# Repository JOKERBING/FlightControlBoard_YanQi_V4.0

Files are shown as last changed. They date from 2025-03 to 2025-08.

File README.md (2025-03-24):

# YanQi Flight Control Board V4.0

**2 x IMU & Baro & 4 x ESC small size PX4 for MAV research.**

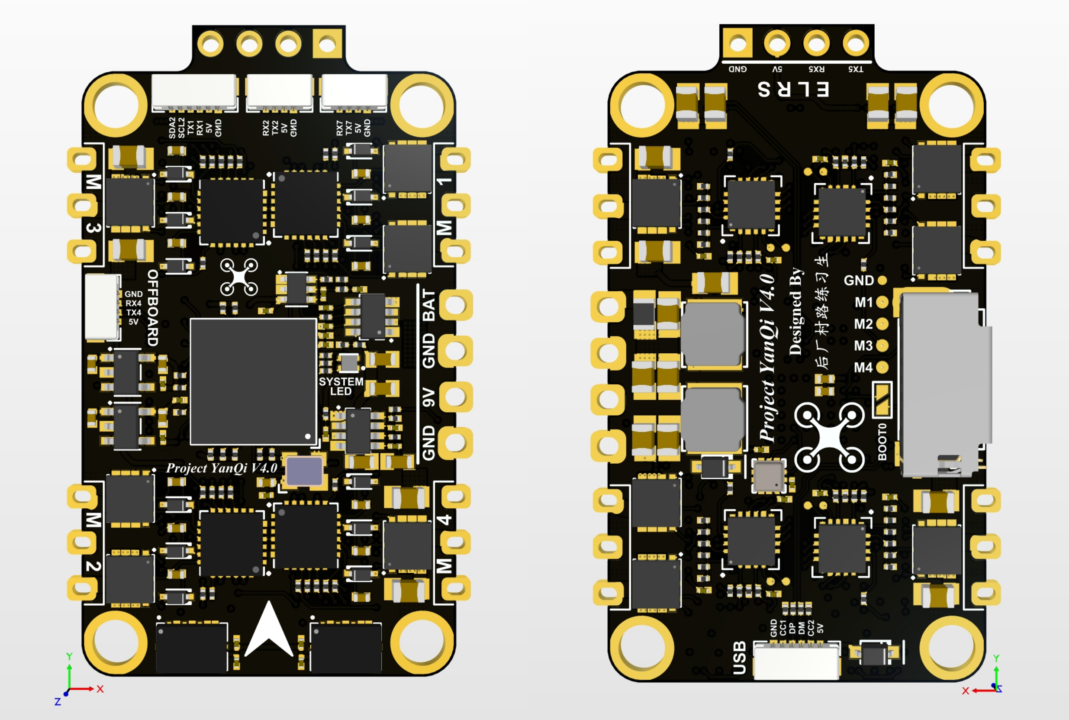
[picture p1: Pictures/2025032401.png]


## Physical

- Mounting: 20 x 35 mm, Φ 2 mm
- Dimensions: 24 x 42.4 x 6 mm
- Weight: 4.9 g

## Specifications

- MCU: STM32H743VIH6, 480MHz, 2MB Flash
- IMU: BMI088 + BMI088
- Baro: BMP388
- ESC: 4 x Bluejay
- MicroSD Card Slot
- USB
- 5 x UART
- 4 x PWM (DShot)
- 1 x External I2C
- 2 x ADC (Battery Voltage, Battery Current)
- BEC 9V 3A output
- BEC 5V 3A output

## UART Mapping

<div align="center">

| UART | TTY | SerialName | Suggest Funcion | DMA |
| :--: | :-: | :---: | :---: | :-: |
| USART1 | /dev/ttyS0 | GPS1 | GPS | OFF |
| USART2 | /dev/ttyS1 | TEL1 | Data Link | ON |
| UART4 | /dev/ttyS3 | TEL2 | Offboard PC | ON |
| UART5 | /dev/ttyS4 |  RC  | ELRS Receiver | ON |
| UART7 | /dev/ttyS6 | TEL3 | Optical Flow | ON |

</div>

## Getting Start

### Compile Locally

Follow the PX4 standard approach.

#### Bootloader:

```shell
make UCAS_YanQiH7_bootloader
```

#### Firmware:

```shell
make UCAS_YanQiH7_default
```

### Burn Bootloader & Firmware

#### Bootloader:

**Method 1：**

 To enter DFU mode, pull up BOOT0 while connecting the USB cable to your computer.

```shell
make UCAS_YanQiH7_bootloader upload
```

**Method 2：**

 To enter DFU mode, pull up BOOT0 while connecting the USB cable to your computer.

```shell
dfu-util -a 0 --dfuse-address 0x08000000 -D ./build/UCAS_YanQiH7_bootloader/UCAS_YanQiH7_bootloader.bin
```

If the burning tool is not installed, install the dfu util burning toolkit first.

```
sudo apt install dfu-util
```

#### Firmware:

**Method 1：**

```shell
make UCAS_YanQiH7_default upload
```

Connect the flight controller directly to your computer via USB.

The firmware will then proceed through a number of upgrade steps (downloading new firmware, erasing old firmware etc.). Each step is printed to the screen.

Once the firmware has completed loading, the device/vehicle will reboot and reconnect.

**Method 2：**

Start QGroundControl and connect the vehicle.

Select **"Q" icon** > **Vehicle Setup** > **Firmware** (sidebar) to open Firmware Setup.

Connect the flight controller directly to your computer via USB.

Check **Advanced settings** and select the version from the dropdown list.

Select the **Custom Firmware file...** option to install the custom firmware for the flight controller (autodetected).

Click the **OK** button to start the update.

The firmware will then proceed through a number of upgrade steps (downloading new firmware, erasing old firmware etc.). Each step is printed to the screen and overall progress is displayed on a progress bar.

Once the firmware has completed loading, the device/vehicle will reboot and reconnect.

## Setting Up PX4 Configuration Settings

### Power

### MAVLink

### Receiver

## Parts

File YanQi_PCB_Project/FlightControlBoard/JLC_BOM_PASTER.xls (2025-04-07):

型号 | 封装 | 位号 | 元件编号
BMI088 | LGA-16_L4.5-W3.0-P0.50-BL | U10,U11 | C194919
RT9013-33GB | SOT-23-5 | U15,U16 | C47773
MP2225GJ-Z | SOT-23-8 | U13,U14 | C133066
STM32H743VIH6 | BGA-100_L8.0-W8.0-P0.80-R10-C10-BL | U1 | C964146
1nF | C0201 | C52 | C161371
1uF | C0402 | C17,C18,C19,C20,C21,C22,C23,C24,C25,C26,C27,C28,C45,C46,C48,C49 | C52923
140kΩ | R0201 | R89 | C158804
1N5819WS | SOD-323 | D13,D14 | C191023
X1G004171002700 | OSC-SMD_4P-L2.5-W2.0-BL | X1 | C255993
INA199A1DCKR | SOT-323-6 | U17 | C59135
2.2uF | C0402 | C2,C3 | C342966
SM04B-XSRS-ETB(LF)(SN) | CONN-SMD_4P-P0.6 | J3,J5,J6 | C5223639
1kΩ | R0201 | R6,R7,R8,R9 | C138165
56Ω | R0201 | R95 | C320971
FC-B1010RGBT-HG | LED-ARRAY-SMD_4P-L1.0-W1.0-TR-RD | LED1 | C158099
22uF | C0603 | C36,C37,C38,C39 | C2762594
FD6288Q | QFN-24_L4.0-W4.0-P0.50-BL-EP2.6 | U6,U7,U8,U9 | C328453
100nF | C0201 | C5,C7,C8,C9,C10,C11,C12,C13,C14,C15,C16,C29,C30,C31,C32,C33,C34,C35,C40,C41,C42,C43,C44,C47,C50,C51 | C160831
BMP388 | LGA-10 | U12 | C779278
AON7934 | DFN-8 | Q1,Q2,Q3,Q4,Q5,Q6,Q7,Q8,Q9,Q10,Q11,Q12 | C485677
22uF | C0805 | C53,C54,C55,C56,C57,C58,C59,C60,C61,C62,C63,C64,C65,C66,C67,C68,C69,C70 | C45783
10mΩ | R0805 | R96 | C163089
22Ω | R0201 | R50,R51,R52,R53,R54,R55,R56,R57,R58,R59,R60,R61,R62,R63,R64,R65,R66,R67,R68,R69,R70,R71,R72,R73,R85,R86 | C155743
74kΩ | R0201 | R90 | C851792
SM06B-XSRS-ETB(LF)(SN) | CONN-SMD_6P-P0.6 | J1,J2 | C5306600
5.1kΩ | R0201 | R83,R84 | C274341
100kΩ | R0201 | R91,R92,R94 | C270364
TF-027-H300 | TF-SMD_HYCW104-TF08-375B | SD1 | C5310495
FHD4020S-100MT | IND-SMD_L4.0-W4.0 | L1 | C602032
FHD4020S-4R7MT | IND-SMD_L4.0-W4.0 | L2 | C602031
10kΩ | R0201 | R1,R2,R3,R4,R5,R10,R11,R12,R13,R14,R15,R16,R17,R18,R19,R20,R21,R22,R23,R24,R25,R78,R79,R80,R81,R82,R87,R88,R93 | C473048
4.7kΩ | R0201 | R27,R29,R31,R33,R35,R37,R39,R41,R43,R45,R47,R49,R74,R75,R76,R77 | C270346
15pF | C0201 | C6 | C161407
1uF | C0201 | C4 | C237278
47kΩ | R0201 | R26,R28,R30,R32,R34,R36,R38,R40,R42,R44,R46,R48 | C270345
4.7uF | C0402 | C1 | C23733
EFM8BB21F16G | QFN-20_L3.0-W3.0-P0.50-BL-EP1.7_EFM8BB21F16G | U2,U3,U4,U5 | C80713
1N4148WTT4 | SOD-523 | D1,D2,D3,D4,D5,D6,D7,D8,D9,D10,D11,D12 | C68948
BurnPad | BURNPAD_0.8MM | P10,P11,P12,P13 | NC
ShortCircuitPad | SHORTCIRCUITPAD | P1 | NC
M3_HOLE | M3_HOLE | H1,H2,H3,H4 | NC
MotorPad | MOTORHALFHOLE | P14,P15,P16,P17,P18,P19,P20,P21,P22,P23,P24,P25 | NC
Power_Pad | POWERHALFHOLE | P26,P27,P28,P29 | NC
型号 | 封装 | 位号 | NC
ZX-SH1.0-4PWT | ELRSPAD | J4 | NC
BurnPad | BURNPAD_0.5MM | P2,P3,P4,P5,P6,P7,P8,P9,P30 | NC

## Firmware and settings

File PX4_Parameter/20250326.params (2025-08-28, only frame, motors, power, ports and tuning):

1	1	BAT1_A_PER_V	1.936521768569946289	9
1	1	BAT1_CAPACITY	-1.000000000000000000	9
1	1	BAT1_I_CHANNEL	-1	6
1	1	BAT1_N_CELLS	3	6
1	1	BAT1_R_INTERNAL	-1.000000000000000000	9
1	1	BAT1_SOURCE	0	6
1	1	BAT1_V_CHANNEL	-1	6
1	1	BAT1_V_CHARGED	4.449999809265136719	9
1	1	BAT1_V_DIV	10.926829338073730469	9
1	1	BAT1_V_EMPTY	3.000000000000000000	9
1	1	BAT1_V_LOAD_DROP	0.300000011920928955	9
1	1	BAT_AVRG_CURRENT	15.000000000000000000	9
1	1	BAT_CRIT_THR	0.070000000298023224	9
1	1	BAT_EMERGEN_THR	0.050000000745058060	9
1	1	BAT_LOW_THR	0.150000005960464478	9
1	1	BAT_N_CELLS	3	6
1	1	BAT_V_CHARGED	4.050000190734863281	9
1	1	BAT_V_EMPTY	3.500000000000000000	9
1	1	BAT_V_LOAD_DROP	0.300000011920928955	9
1	1	BAT_V_OFFS_CURR	0.000000000000000000	9
1	1	CA_ROTOR0_PX	0.053500000387430191	9
1	1	CA_ROTOR0_PY	0.053500000387430191	9
1	1	CA_ROTOR1_PX	-0.053500000387430191	9
1	1	CA_ROTOR1_PY	-0.053500000387430191	9
1	1	CA_ROTOR2_KM	-0.050000000745058060	9
1	1	CA_ROTOR2_PX	0.053500000387430191	9
1	1	CA_ROTOR2_PY	-0.053500000387430191	9
1	1	CA_ROTOR3_KM	-0.050000000745058060	9
1	1	CA_ROTOR3_PX	-0.053500000387430191	9
1	1	CA_ROTOR3_PY	0.053500000387430191	9
1	1	CA_ROTOR_COUNT	4	6
1	1	MC_PITCHRATE_D	0.004399999976158142	9
1	1	MC_PITCHRATE_FF	0.000000000000000000	9
1	1	MC_PITCHRATE_I	0.300000011920928955	9
1	1	MC_PITCHRATE_K	0.550000011920928955	9
1	1	MC_PITCHRATE_MAX	220.000000000000000000	9
1	1	MC_PITCHRATE_P	0.150000005960464478	9
1	1	MC_PITCH_P	8.000000000000000000	9
1	1	MC_ROLLRATE_D	0.004399999976158142	9
1	1	MC_ROLLRATE_FF	0.000000000000000000	9
1	1	MC_ROLLRATE_I	0.300000011920928955	9
1	1	MC_ROLLRATE_K	0.550000011920928955	9
1	1	MC_ROLLRATE_MAX	220.000000000000000000	9
1	1	MC_ROLLRATE_P	0.150000005960464478	9
1	1	MC_ROLL_P	12.000000000000000000	9
1	1	MC_YAWRATE_D	0.002000000094994903	9
1	1	MC_YAWRATE_FF	0.000000000000000000	9
1	1	MC_YAWRATE_I	0.200000002980232239	9
1	1	MC_YAWRATE_K	1.450000047683715820	9
1	1	MC_YAWRATE_MAX	360.000000000000000000	9
1	1	MC_YAWRATE_P	0.200000002980232239	9
1	1	MC_YAW_P	10.000000000000000000	9
1	1	MC_YAW_WEIGHT	0.400000005960464478	9
1	1	MOT_ORDERING	0	6
1	1	MOT_POLE_COUNT	12	6
1	1	MOT_SLEW_MAX	0.000000000000000000	9
1	1	SYS_AUTOSTART	4001	6

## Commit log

2025-04-06 Fix PCB and SMT Files
    [FlightControlBoard.PrjPcb, FlightControlBoard.xlsx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]
2025-04-07 Add JLC BOM Files
    [JLC_BOM_PASTER.xls]
2025-08-28 添加Betaflight固件
2025-08-28 添加PX4固件和参数
    [20250326.params]
2025-08-28 删除PCB中电调固件烧录触点部分，优化走线
    [ESC.SchDoc, FlightControlBoard.PrjPcb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]
